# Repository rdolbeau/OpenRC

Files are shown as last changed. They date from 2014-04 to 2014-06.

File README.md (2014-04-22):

OpenRC Logo

This if a fork of https://github.com/bryancostanich/OpenRC, where I can add some notes from my experience building the OpenRC truggy designed by Daniel Noree (see https://plus.google.com/communities/112745535856143176146).

Repo for the OpenRC Printable Radio Controlled Vehicles Project. Contains printable parts, instructions, and parts sourcing info. Based on the [Google Group here](https://plus.google.com/communities/112745535856143176146)

# [General RC Information](https://github.com/bryancostanich/OpenRC/blob/master/RCInfo.md)
Battery info, radio info, etc.

# Projects

## [Truggy](https://github.com/bryancostanich/OpenRC/tree/master/Truggy)

An awesome 4WD 1:10 Scale 3D printable truggy! This pic says all about this sexy beast:

Truggy Pic

## [Touring Car](https://github.com/bryancostanich/OpenRC/tree/master/Touring_Car)

4WD 1:10 scale 3D Printable touring car. Also designed by Daniel, the Touring Car was his first attempt at designing an RC Car.

Touring Car Pic

## [Ducted Fan Design Library](https://github.com/bryancostanich/OpenRC/tree/master/DuctedFanDesignLibrary)

An electric ducted fan design library written in Python using the Blender API. Currently, the software is in script form, but an add-on of sorts is being created.

Fan

## Authors
 * Truggy - Daniel Norée
 * Ducted Fan Design Library - André Roy

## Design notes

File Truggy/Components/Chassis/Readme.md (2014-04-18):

This is the chassis. You'll need one of each:

 * Chassie Plate Front.B.0.stl
 * Chassie Plate Rear.B.0.stl
 * Left Shield.A.5.stl
 * Right Shield.A.6.stl
 * Top Deck Front.B.6.stl
 * Top Deck Rear.B.6.stl

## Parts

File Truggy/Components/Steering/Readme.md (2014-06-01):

In here in the steering system

 * Steering Block.B.4.stl: You'll need 2 of those (one for each wheel)
 * Steering_Pin.A.0.stl: You'll need 2 of those (one for each side)
 * Updated Steering.A.3.stl: Many elements in one go, you'll only need one. One of the parts already has built-in support. If you need to replace one of the parts, or want your own support, you'll need to regenerate the STL from the original STEP file in a CAD program rather than print this.

You'll also need a servo holder for the servo (see in ../Electronics Holders).

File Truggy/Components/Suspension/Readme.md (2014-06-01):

Some stuff related to the suspension subsystem.

 * Shock Spacer .A.0.stl, Shock Spacers x4.A.0.stl : Includes 4 spacers to attach your shocks. Print one or the other, differences unknown. (the x4 is supposed to be newer, I believe)
 * Shock Tower New.A.3.stl, Shock Tower Rear.A.5.stl, Shock Tower Front.A.4.stl : Various Shock Towers (where the fixed ends of the shocks are attached, the other ends go on the wishbones). You need a tower at the front and the back. At the moment, my truggy uses the 'New.A.3' Tower. 
 * Wishbone  Front.B.0.stl, Wishbone  Rear.B.0.stl, Wishbone Test Front.A.2.stl, Wishbone Test Rear.A.2.stl : Wishbones for the suspension. You need 2 fronts and 2 rears. The STEP file uses A.2, but B.0 are supposed to be newer and sturdier.

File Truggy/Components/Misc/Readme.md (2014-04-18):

ome more indispensible stuff.

 * C-Hub.B.1.stl: to carry the front steering block, you'll need 2
 * Central Drive Shaft Joint & Input Gear.A.3.stl
 * OpenRC Truggy Rim.B.4.stl: rim for the wheel, one per wheel (you'll also need tires)
 * Rear C-Hub.B.2.stl: to carry the rear wheel, you'll need 2
 * Spur Gear 20T.B.0.stl: goes on the motor, just the one (plus spares :-)
 * Turnbuckle Front.B.1.stl: part of the front suspension, need 2
 * Turnbuckle Rear.B.0.stl: part of the rear suspension, need 2
 * Turnbuckle Spacer x4.A.0.stl: helps with the turnbuckles, already a group of 4
 * Wheel Spacer x4.A.1.stl: hexagonal 12mm wheel nuts, already a group of 4

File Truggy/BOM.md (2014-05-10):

# Truggy Bill of Materials

## Hardware

### Screws
 * (2) Hexagon Socket Countersunk Head Screw ISO 10642 - M3 x 6 (front and back differential assembly)
 * (54) Hexagon Socket Countersunk Head Screw ISO 10642 - M3 x 8 
 * (8) Hexagon Socket Countersunk Head Screw ISO 10642 - M3 x 12
 * (4) Hexagon Socket Countersunk Head Screw ISO 10642 - M3 x 16
 * (10) Hexagon Socket Pan Head Cap Screw ISO 7380 - M3 x 8
 * (10) Hexagon Socket Pan Head Cap Screw ISO 7380 - M3 x 10
 * (12) Hexagon Socket Pan Head Cap Screw ISO 7380 - M3 x 12
 * (4) Hexagon Socket Pan Head Cap Screw ISO 7380 - M3 x 14
 * (4) Hexagon Socket Pan Head Cap Screw ISO 7380 - M3 x 16
 
#### Screw Sources

 * [M3 Hexagon Socket Countersunk Head Screw, various materials and lengths @ Amazon Supply](http://www.amazonsupply.com/s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)
 * [ISO 7380 M3 Button (Pan) Head Cap Screws, various materials and lengths @ Amazon Supply](http://www.amazonsupply.com/s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)
 
###  Nuts

 * (26) M3 Hexagon Nut ISO 4032 - [Amazon Source](http://www.amazon.com/dp/B000FN0CP0/ref=biss_dp_t_asn)
 
### Bearings
 * (10) 10x15x4 - [Amazon Supply Source](http://www.amazonsupply.com/s/ref=sp_search?guess=true&Action=submit&keywords=10x15x4+bearing), also known as 6700 zz (when shielded) or 6700 2rs (when sealed)
 * (8) 5x10x4 - [Amazon Supply Source](http://www.amazonsupply.com/s/ref=sp_search?guess=true&Action=submit&keywords=5x10x4+bearing), also known as MR105 ZZ (when shielded) or MR105 2RS (when sealed)
 * (4) 6x12x4 - [Amazon Supply Source](http://www.amazonsupply.com/s/ref=sp_search?guess=true&Action=submit&keywords=6x12x4+bearing), also known as MR126 ZZ (when shielded) or MR126 2RS (when sealed)

### Rods
 * (4) Diam 2.0 x 32mm
 * (3) Diam 3.0 x 18mm (for the differentials)
 * (4) Diam 3.0 x 56mm (for the wishbones)
 * Optional: Diam 2.0 x 10mm for internal driveshafts (2 for each printed driveshafts, or see below for prebuilt metal shafts from Conrad)

### Ball Head Screws
 * (5 or 6?) 5mm Ball Head Screws such as HSP 02038?
 
### Drivetrain
 * (4) Outer Driveshafts - CVD 1:10 118MM (See sources)
 
### Wheels
 * (4) Rims - Printed OpenRC
 * (4) Tires - Losi 320S Zombie Max Tire with Foam LOSB7213
 
### Suspension
 * (4) 100mm Standard RC Car Shocks
 	* [Blue Aluminum @ HobbyKing.com](http://www.hobbyking.com/hobbyking/store/__22499___1_10_Model_Car_100mm_Adjustable_Aluminum_Shock_Absorber_2pc_Blue_.html)
 	* [Purple Aluminum @ HobbyKing.com](http://www.hobbyking.com/hobbyking/store/__26276__1_10_Car_100mm_Aluminum_Shock_Absorber_Purple_2pcs_bag_.html)
 	* [Silver Aluminum @ HobbyKing](http://www.hobbyking.com/hobbyking/store/__22500__1_10_Model_Car_100mm_Adjustable_Aluminum_Shock_Absorber_2pc_.html)
 	* [Gun Metal Aluminum with Three Pairs of Various Strength Spings @ TowerHobby.com](http://www3.towerhobbies.com/cgi-bin/wti0001p?&I=LXDCTM&P=7)
 
###  Body
 * Body - HPI Firestorm DSX-1 Lexan Truck Body HPI7123
 
## RC Components

### Motor + Electronic Speed Controller (ESC)
Standard 1:10  motor rated for 4WD.

 * [Castle Creations SV3 Sidewinder 6900kV @ TowerHobbies.com](http://www3.towerhobbies.com/cgi-bin/wti0001p?&I=LXDAVR&P=7)
 * [Castle Creations SV3 Sidewidner 7700kV @ TowerHobbies.com](http://www3.towerhobbies.com/cgi-bin/wti0001p?&I=LXDAVS&P=7)
 * [OUT OF STOCK - Turnigy TrackStar Waterproof 1/10 Brushless Power System 4000KV/80A (Motor+ESC Combo)](http://www.hobbyking.com/hobbyking/store/uh_viewItem.asp?idProduct=25138 @ HobbyKing.com)

### Battery

 * [Turnigy 4000mAh 2S 40C Lipo Pack @ HobbyKing.com](http://www.hobbyking.com/hobbyking/store/RC_PRODUCT_SEARCH.asp?strSearch=Turnigy+4000mAh+2S+40C)

### Battery Charger

 * [Ace T6DC Digital Multi Charger @ TowerHobbies.com](http://www3.towerhobbies.com/cgi-bin/wti0001p?&I=LXBFDR&P=7)

### Servo

 * [BMS-620MG High Torque Servo (Metal Gear) 9.1kg / .15sec / 50g](http://www.hobbyking.com/hobbyking/store/RC_PRODUCT_SEARCH.asp?strSearch=BMS-620MG)

### Radio

Standard 2 Channel Transmitter and Receiver (Radio System)

 * [Hobby King GT-2 2.4Ghz 2Ch Radio System](http://www.hobbyking.com/hobbyking/store/RC_PRODUCT_SEARCH.asp?strSearch=Hobby+King+GT-2+2.4Ghz+2Ch)
 * [Tower Hobbies 224 2-channel 2.4ghz Radio System](http://www3.towerhobbies.com/cgi-bin/wti0001p?&I=LXWPW0&P=7)
 * [Tactic TTX240 2-Channel SLT 2.4ghz Radio System @ TowerHobbies.com](http://www3.towerhobbies.com/cgi-bin/wti0001p?&I=LXWRP3&P=7)
 * [HPI Racing TF-40 2.4ghz Radio System @ TowerHobbies.com](http://www3.towerhobbies.com/cgi-bin/wti0001p?&I=LXCEHR&P=7)
 * [Axial AX-3 2-Channel 2.4ghz Radio System @ TowerHobbies.com](http://www3.towerhobbies.com/cgi-bin/wti0001p?&I=LXBMCM&P=7)
 
### Shafts
 * CVD (between diff & wheels) [Conrad](http://www.conrad.com/ce/en/product/231121/)
 * Drive shafts (between central and front/read diff, optional, can be printed) [Conrad] (http://www.conrad.com/ce/en/product/223477/)

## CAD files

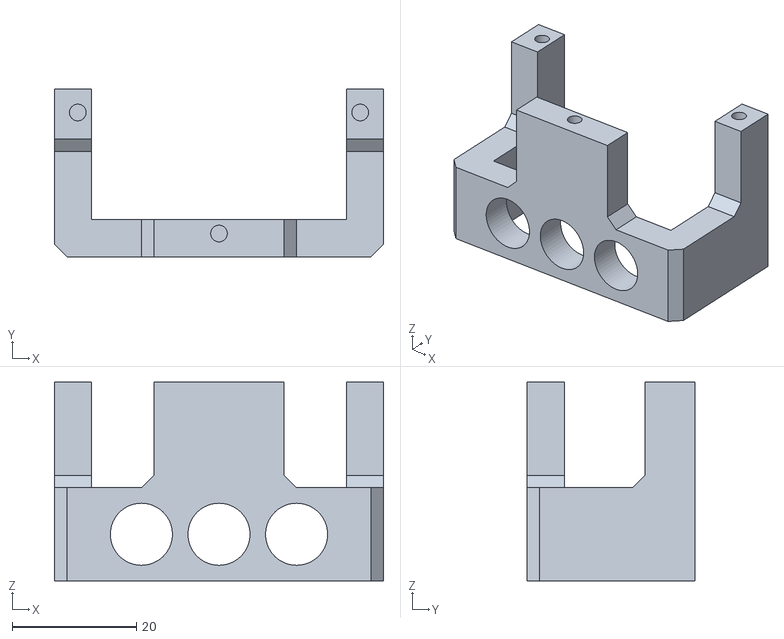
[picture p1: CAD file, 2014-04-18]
Truggy/Components/Electronics Holders/Servo Holder for BMS-620MG Servo.B.1.stl
53.0 x 27.0 x 32.0

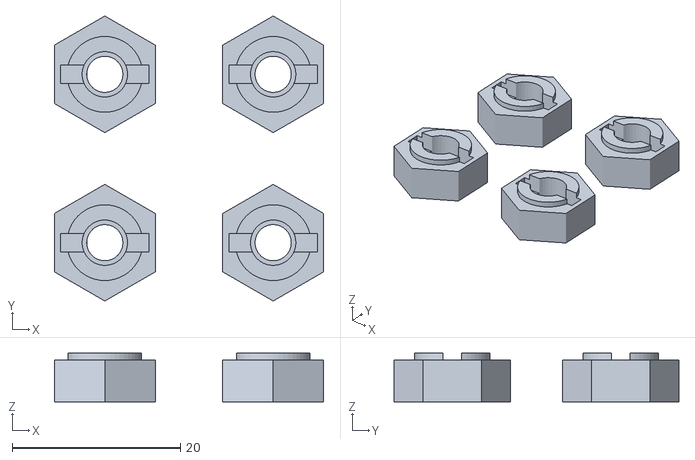
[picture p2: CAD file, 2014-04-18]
Truggy/Components/Misc/Wheel Spacer x4.A.1.stl
32.0 x 33.9 x 5.80

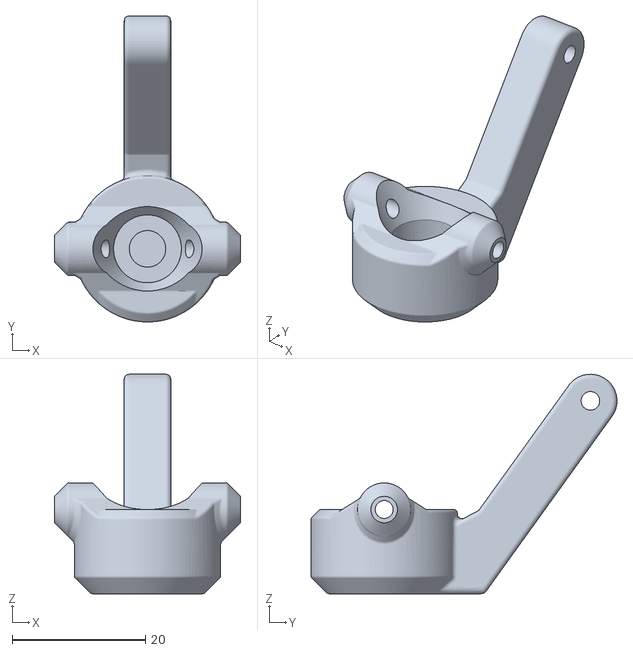
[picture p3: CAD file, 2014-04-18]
Truggy/Components/Steering/Steering Block.B.4.stl
28.0 x 46.0 x 33.0

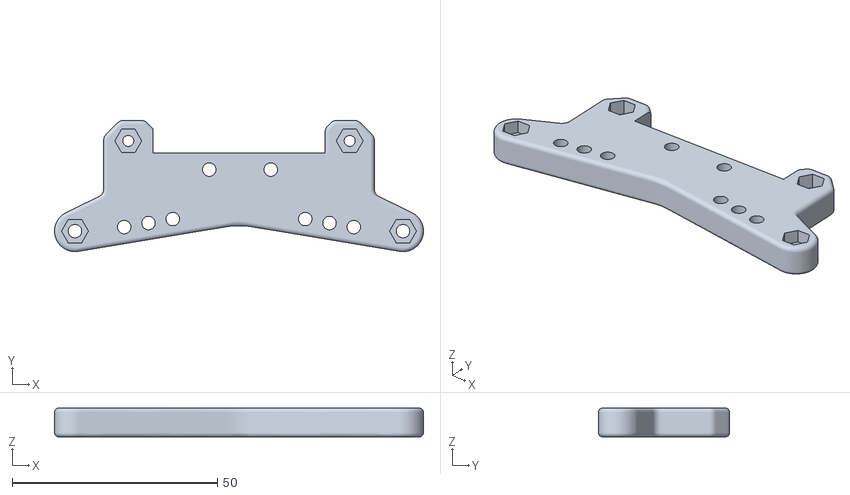
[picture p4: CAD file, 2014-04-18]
Truggy/Components/Suspension/Shock Tower New.A.3.stl
90.0 x 32.0 x 7.00

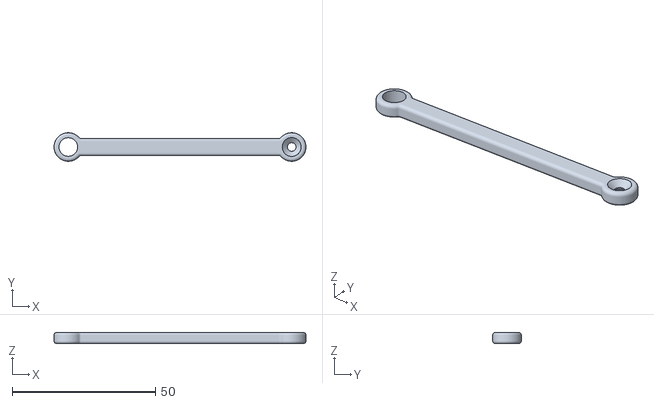
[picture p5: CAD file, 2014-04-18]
Truggy/Components/Misc/Turnbuckle Rear.B.0.stl
88.0 x 9.99 x 4.00

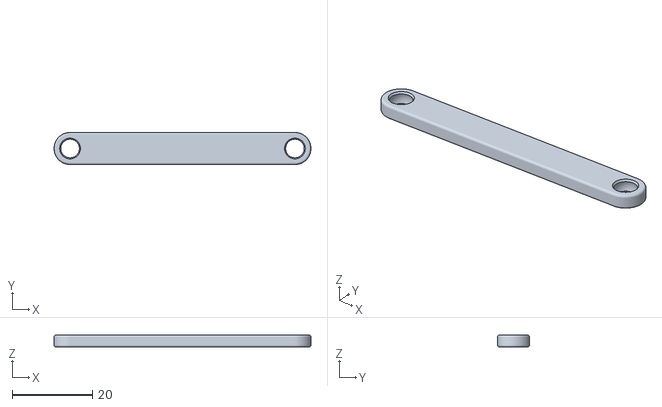
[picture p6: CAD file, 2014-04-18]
Truggy/Components/Steering/Steering_Pin.A.0.stl
64.0 x 8.00 x 3.00

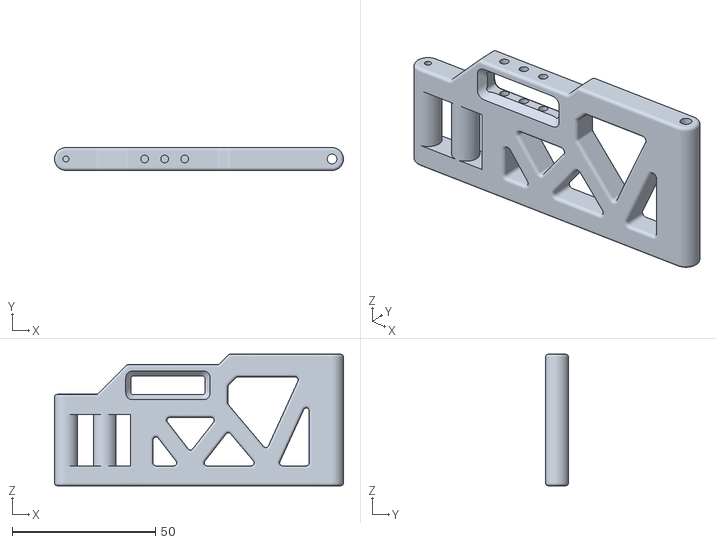
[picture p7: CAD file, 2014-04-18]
Truggy/Components/Suspension/Wishbone Test Front.A.2.stl
101.0 x 8.00 x 46.0

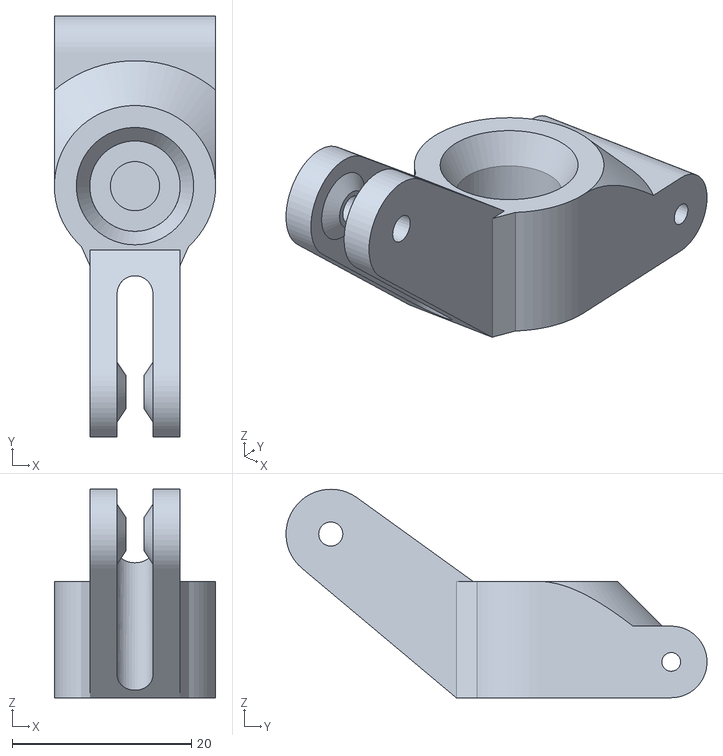
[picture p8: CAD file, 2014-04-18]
Truggy/Components/Misc/Rear C-Hub.B.2.stl
18.0 x 47.0 x 23.3

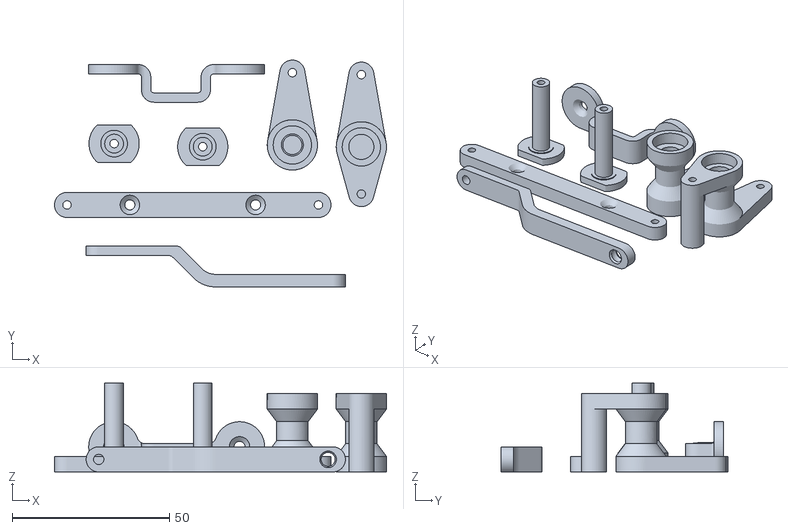
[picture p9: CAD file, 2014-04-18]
Truggy/Components/Steering/Updated Steering.A.3.stl
105.6 x 72.2 x 28.3

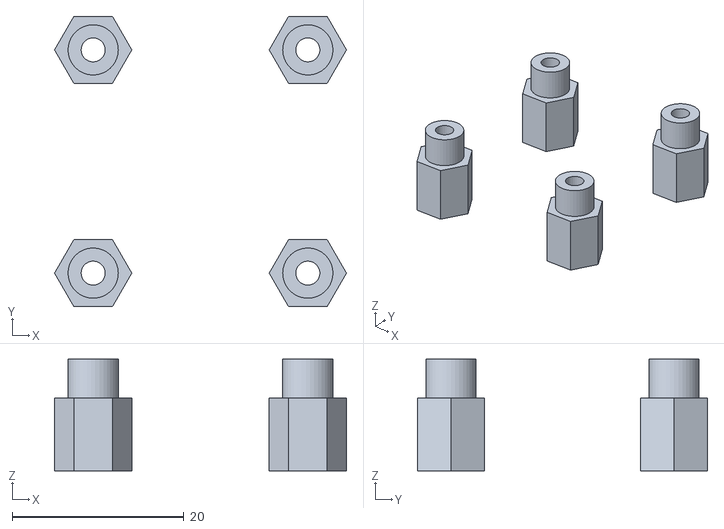
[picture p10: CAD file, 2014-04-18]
Truggy/Components/Suspension/Shock Spacer .A.0.stl
34.0 x 33.8 x 13.0

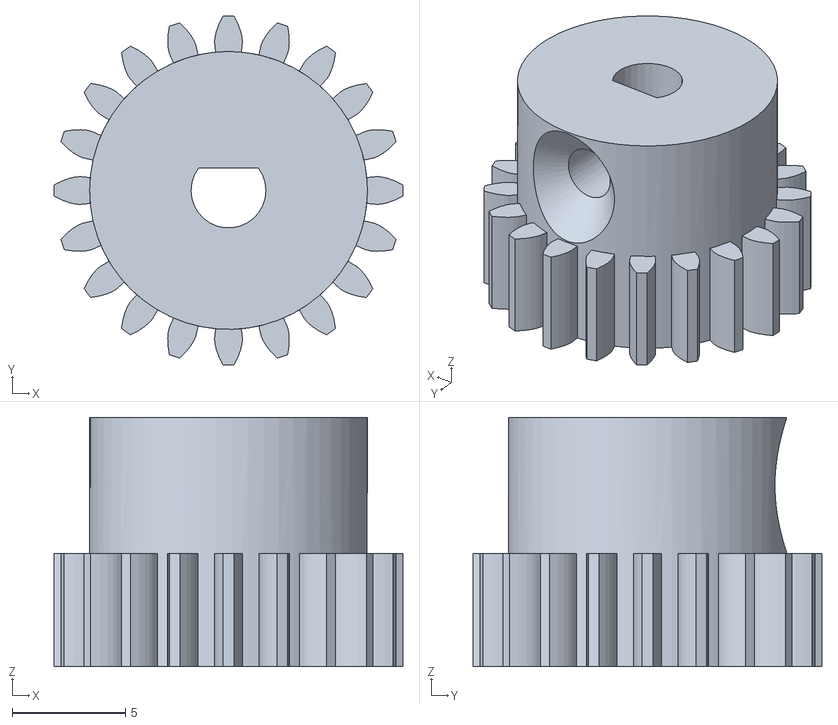
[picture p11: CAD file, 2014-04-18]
Truggy/Components/Misc/Spur Gear 20T.B.0.stl
15.4 x 15.4 x 11.0

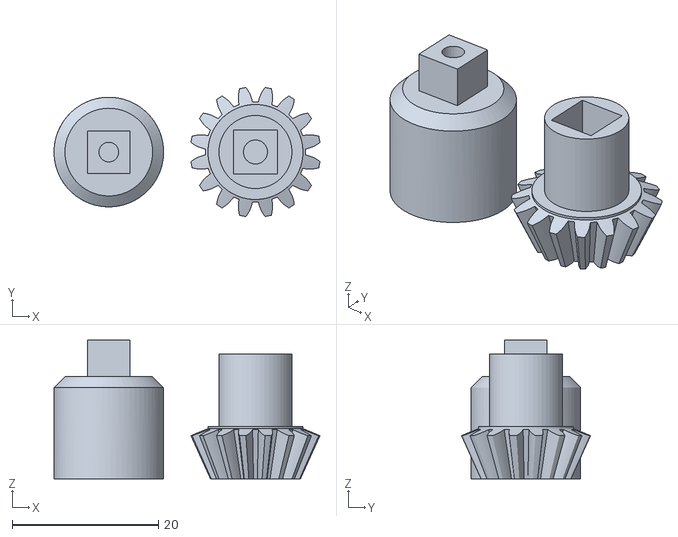
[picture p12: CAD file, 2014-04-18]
Truggy/Components/Misc/Central Drive Shaft Joint & Input Gear.A.3.stl
36.4 x 17.7 x 19.0

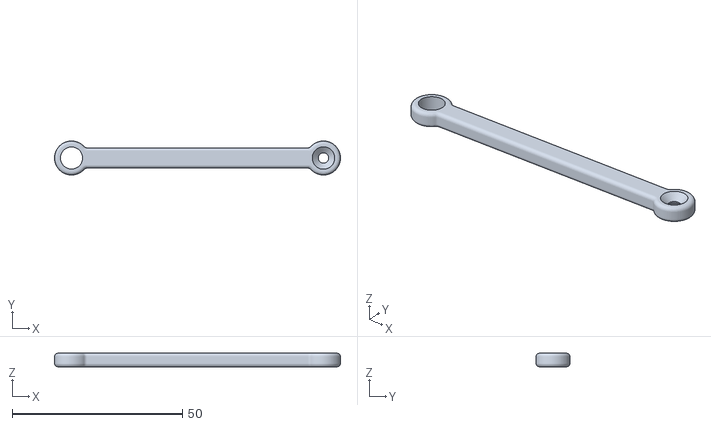
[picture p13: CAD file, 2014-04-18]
Truggy/Components/Misc/Turnbuckle Front.B.1.stl
84.0 x 9.99 x 4.00

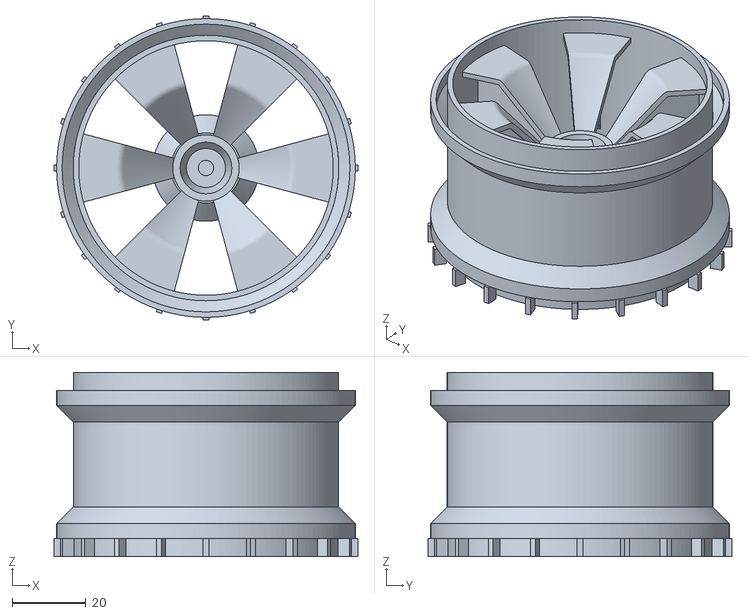
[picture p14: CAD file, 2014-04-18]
Truggy/Components/Misc/OpenRC Truggy Rim.B.4.stl
82.4 x 82.4 x 50.0

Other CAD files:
Truggy/Components/Misc/C-Hub.B.1.stl

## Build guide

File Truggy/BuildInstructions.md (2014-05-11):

# Build Instructions
## Differential
 * [Video](http://www.youtube.com/watch?v=Th_myFCZTWo&feature=youtu.be)

## Chassis
 * You need 5 Countersunk Head Screw M3x8 on each side, to connect the front and back plate to the left and right shield (10 screws in all)
 * You need 4 Countersunk Head Screw M3x8 to connect the back chassis plate to the back differential housing, and 4 Hexagon Nut M3 to go on the sides of the housing (not sure is M3x8 is quite long enough, but that's what's in the CAD file)
 * You need 4 Pan Head Cap Screw M3x10 to connect the fron chassis plate to the front differential housing, and 4 Hexagon Nut M3 to go on the sides of the
 housing
 * You need 6 Countersunk Head Screw M3x8 to connect the front & back chassis plate to the central differential housing

## Steering
 * You need 2 Countersunk Head Screw M3x8 to attach the front chassis plate to the steering columns ; you can use slightly longer screw such as M3x12 but they will be harder to screw properly in the plastic
 * the 4 6x12x4 bearings are used here for the steering system
 * 4 more Countersunk Head Screw M3x8 are required, two to add the upper part to the columns, and two more for the horizontal bar

## Servo Holder
 * You need 3 Countersunk Head Screw M3x8 to attach the front chassis plate to the Servo Holder. Note that the "Servo Holder for BMS-620MG Servo" should fit most standard size servo (it fits a for-testing-only Hitec HS-311).

## Front differential
 * There's a helpful document to assemble the differential itself under "Components/Differential/Documentation/OpenRC Differential Assembly.pdf" (and the video linked above). Each differential use 2 Countersunk Head Screw M3x8, 2 Countersunk Head Screw M3x16 and a Diam 3 x 18 mm pin and 2 10x15x4 bearings
 * First you need to put in the central drive shaft joint & input gear. The pair is assembled by a Pan Head Cap Screw M3x12, and rotates inside a pair of 10x15x4 bearings
 * Then you can put the differential itself in
 * Use 2 Countersunk Head Screw M3x12 to assemble the horizontal bar at the bottom front, beware, the front wishbone and their pins must be put in at this point
 * Use 2 Pan Head Screw M3x16 a the top to assemble the second part of the housing, plus 2 Hexagon Nut M3. Note that you also need assemble the front shock tower at this point, and it has a front and a back so beware
 * Use a Countersunk Head Screw M3x6 to assemble the top to the bottom at the front, above the horizontal bar

## Central differential
 * Same principle than the front & rear differential, but without the shaft joint & input gear (both drive shafts connect to the differential directly). Same list of (non-printed) parts as well.
 * You need to install the front drive shaft at this point (either a printed one with two 2 x 10 mm pin, or just bought one as listed in the BOM), along with putting the central differential in the housing
 * The 4 Countersunk Head Screw M3x12 to assemble the second (top) part of the housing

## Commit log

2014-04-18 Add some newer (and older?) STLs ; improve BOM a bit ; add some build instructions ; add some readmes in subdirectories
    [C-Hub.B.1.stl, Central Drive Shaft Joint & Input Gear.A.3.stl, OpenRC Truggy Rim.B.4.stl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]
2014-04-26 update BOM
2014-05-11 servo holder
